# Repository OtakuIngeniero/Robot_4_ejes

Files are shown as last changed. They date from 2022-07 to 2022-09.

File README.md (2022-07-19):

# Robot_4_ejes
proyecto de robot pick n place de cuatro grados de libertad, 250mm de alcance y 400g de carga maxima a maxima extencion

<p align="center">
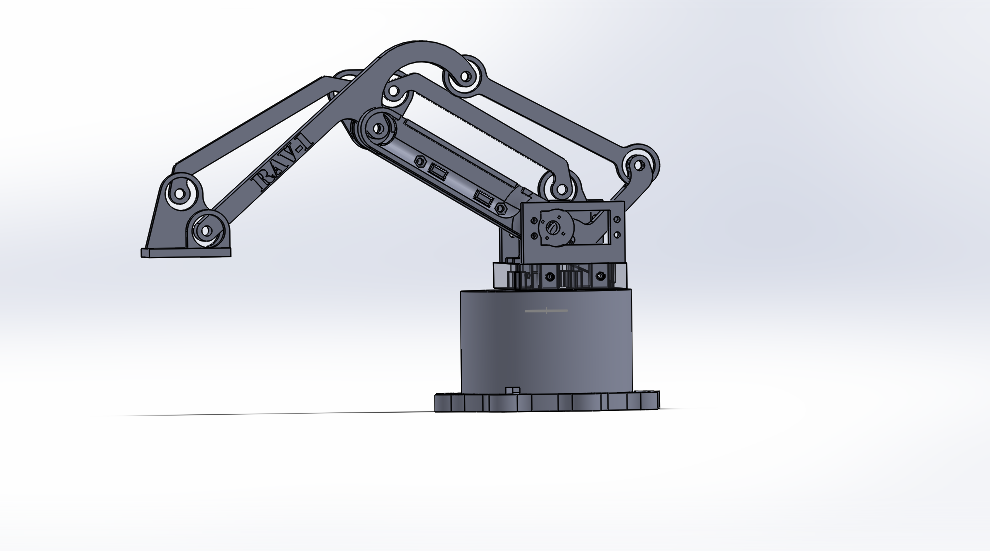
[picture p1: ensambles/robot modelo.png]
hover text
  
</p>

<p align="center">
  
  https://user-images.githubusercontent.com/108755939/179776285-c8175e38-8c07-46ec-a8a5-bc581136b5d1.mp4
  
</p>

- El diseño del robot esta completo y es funcional
- Se midio en un modelo real que cumple las especificaciones planteadas de extencion y carga maxima
- Debido al juego muerto de los motores (1º) el robot tiene en la brida un juego de aproximadamente +-3mm

- Si bien existen muchos controladores para robot mejores y mas completos se me pedia escribir el mio propio para el proyecto, asi que eso hice, el controlador es el modulo "robot", necesita para andar tener instalado sympy

# Lista de compras:

- rodamientos:

15 ----------- Ruleman 6262RS

1 ------------ Ruleman 30202JR /optativo v2 30305

- motores:

3 ------------ Servomotor MG946R

1 ------------ Servomotor SG90

- Controlador:

1 ------------ Arduino nano

- Buloneria:

6 ------------ tornillos de 3/2in con tuercas

18 ----------- tornillos de 1/2in

6 ------------ tornillos de 1in

1 ------------ varilla retificada de 6mm

# TO DO list:
- Darle mas robustez al codigo, principalmente en los puntos no alcanzables
- Hacer un pcb para el arduino porque esta en protoboard
- Comentar y documentar el codigo porque en 1 mes me voy a olvidar de todo

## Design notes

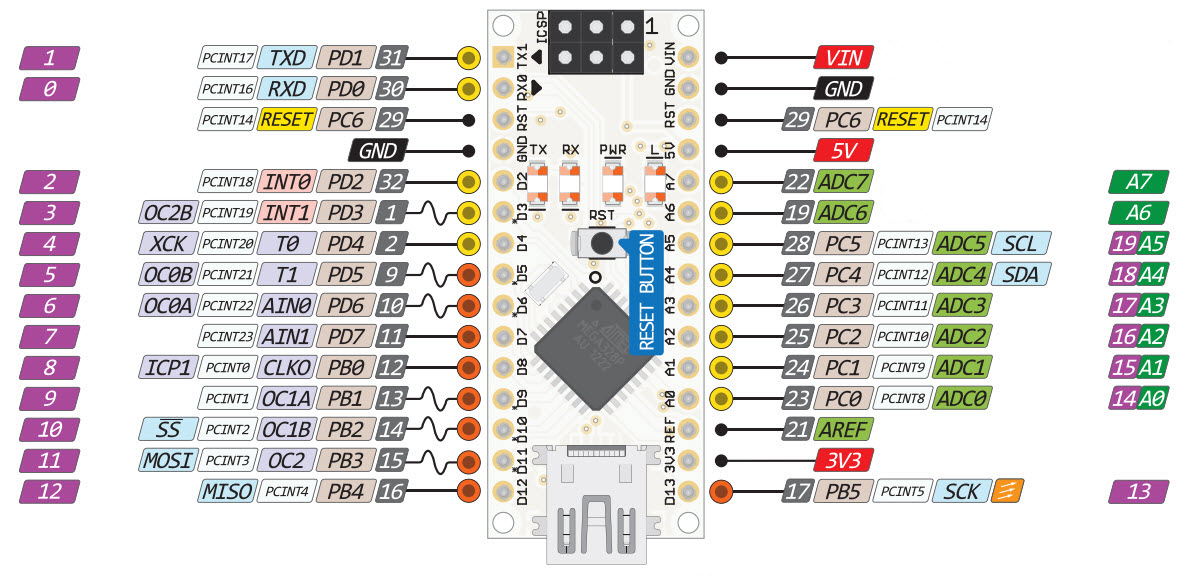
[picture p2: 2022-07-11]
robot irl/arduino nano pinout.jpg

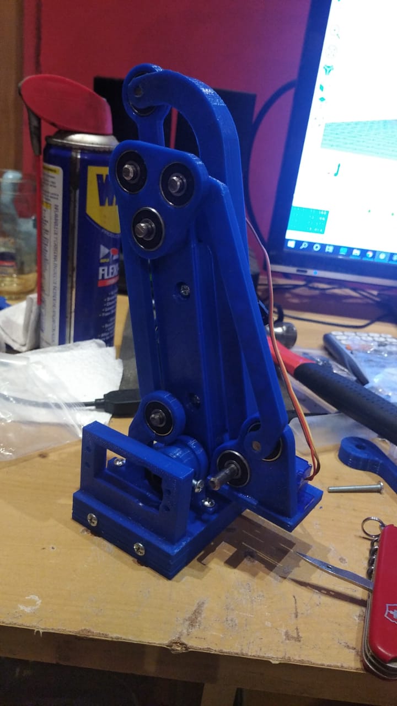
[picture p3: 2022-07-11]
robot irl/img/brazo.jpeg

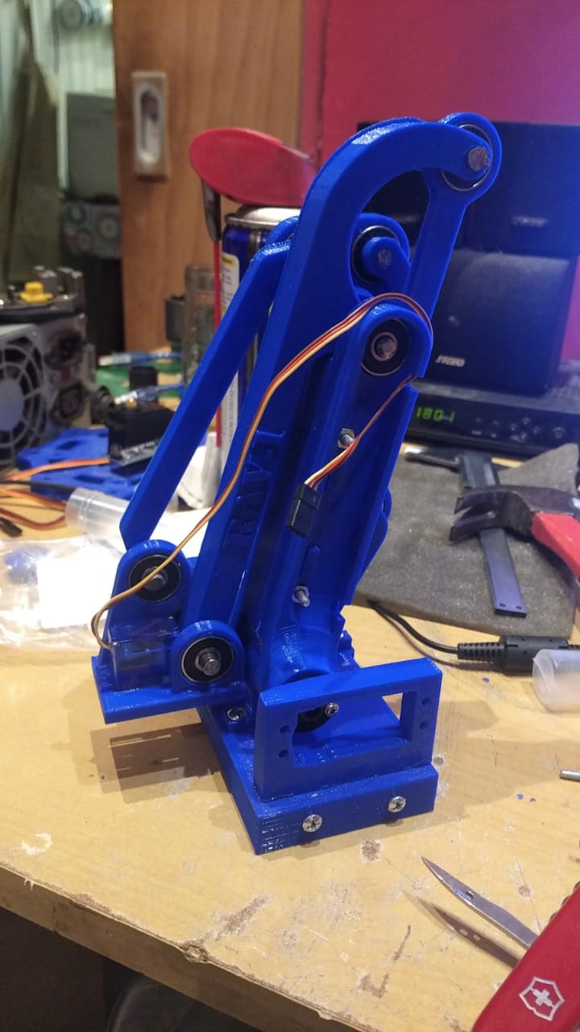
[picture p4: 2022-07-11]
robot irl/img/brazo2.jpeg

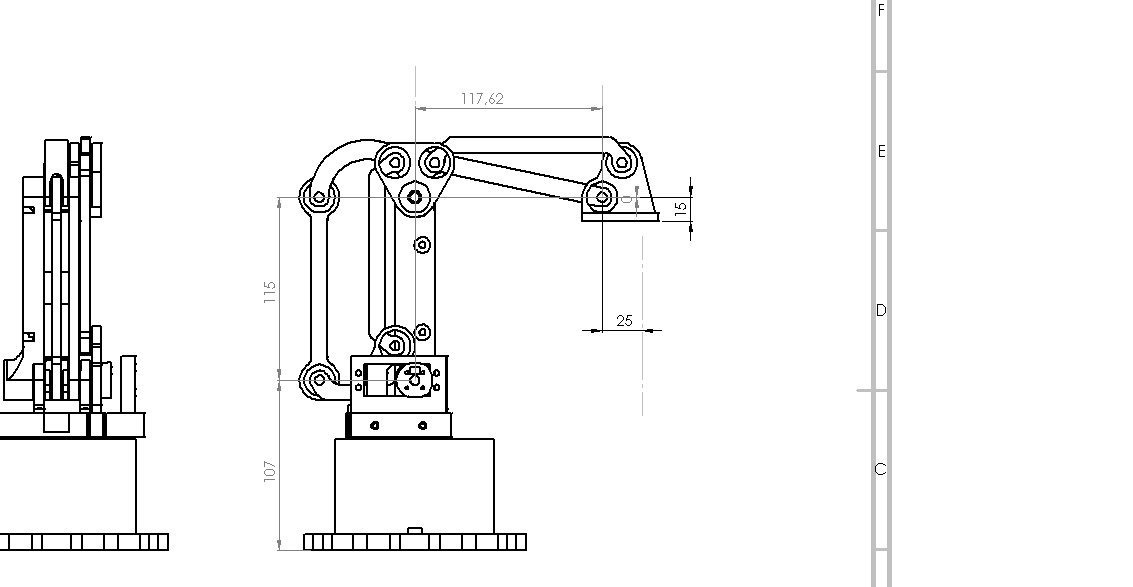
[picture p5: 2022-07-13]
planos/plano_lateral.JPG

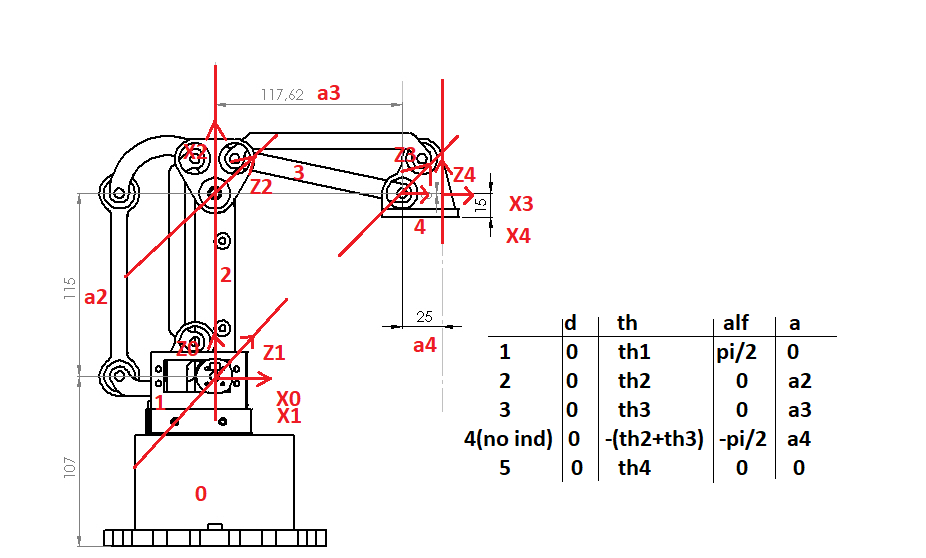
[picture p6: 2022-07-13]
planos/DH_params.png

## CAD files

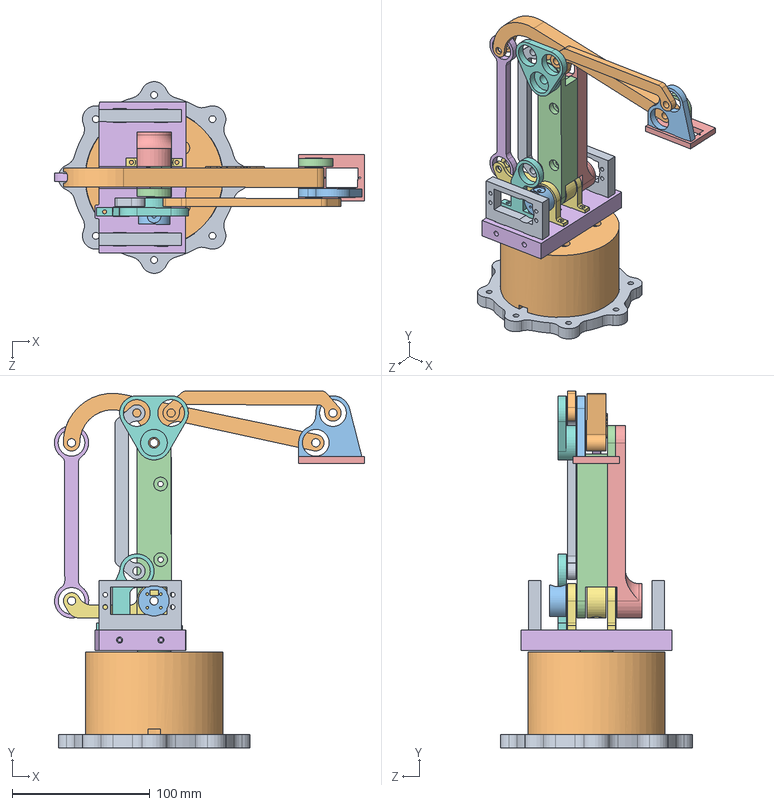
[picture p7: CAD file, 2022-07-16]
ensambles/Ensamble completo.SLDASM
225.7 x 259.7 x 139.3 mm
Base_A
Base_B
Base_C
30202JR
Eje_1_tractor
Eje_1_plataforma
Soporte_eje_2 x 2
Soporte_paralelas
Soporte_motor x 2
Eje_3
Eje_4_A
Eje_4_B
Eje_4_C
Leva_eje_3
Panalca_eje_3
Triangulo
Varilla_115mm
Varilla_117mm
eje_3_tractor
Eje_2_A
Eje_2_B

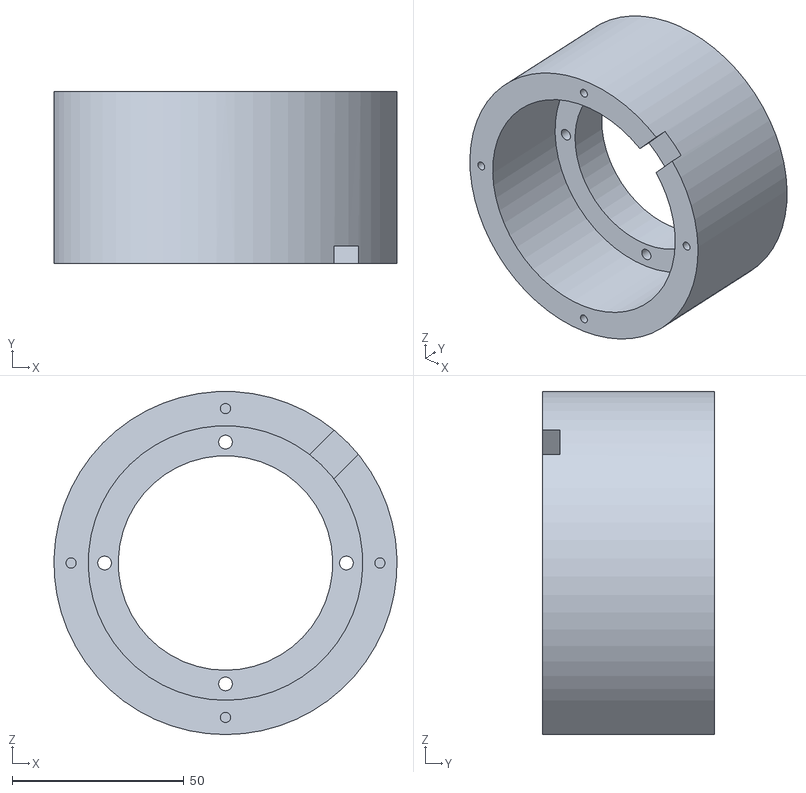
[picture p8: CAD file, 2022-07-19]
imprimibles/base/Base_A_V2.STL
100.0 x 50.0 x 100.0

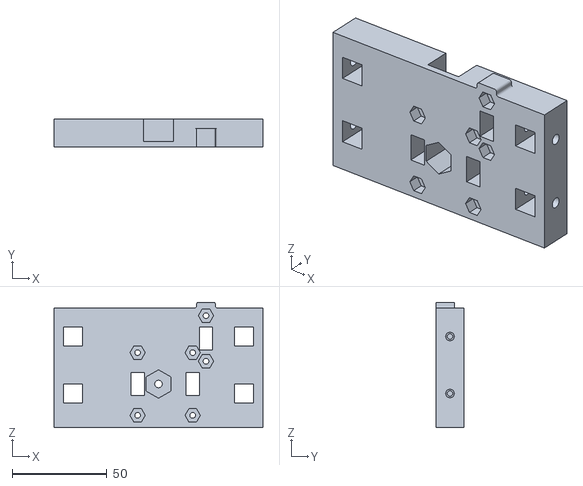
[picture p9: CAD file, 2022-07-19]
imprimibles/eje_1/Eje_1_plataforma_V2.STL
110.0 x 15.0 x 66.0

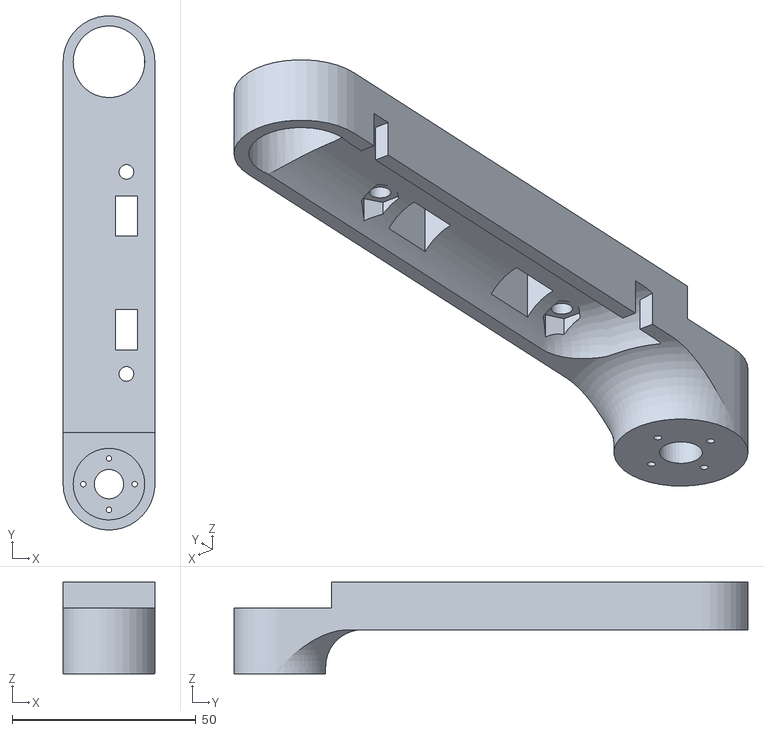
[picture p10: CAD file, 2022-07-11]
imprimibles/eje_2/Eje_2_B_extra_alcance.STL
25.0 x 139.9 x 25.0

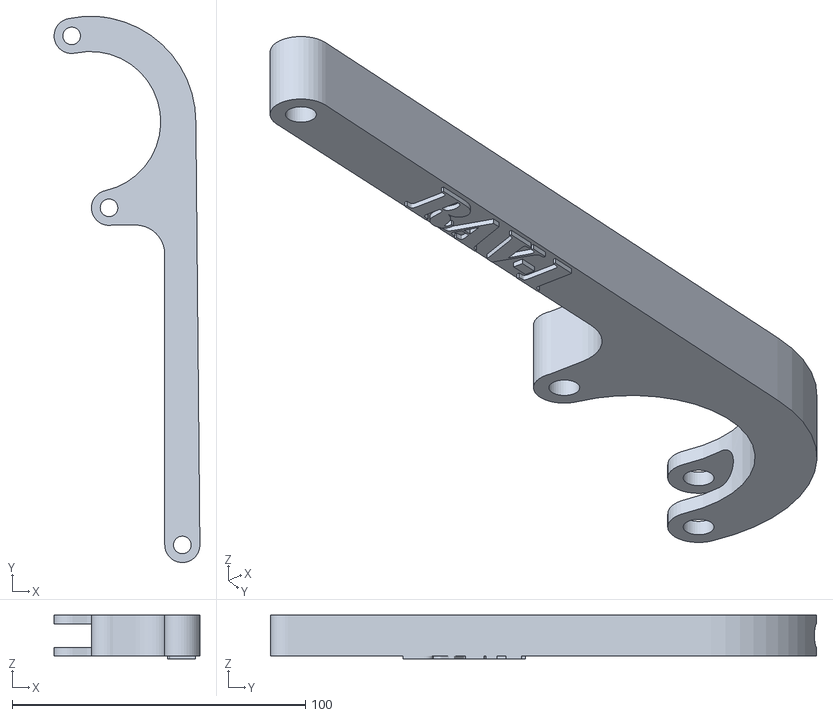
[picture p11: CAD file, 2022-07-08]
imprimibles/eje_3/Eje_3.STL
49.7 x 186.2 x 15.0

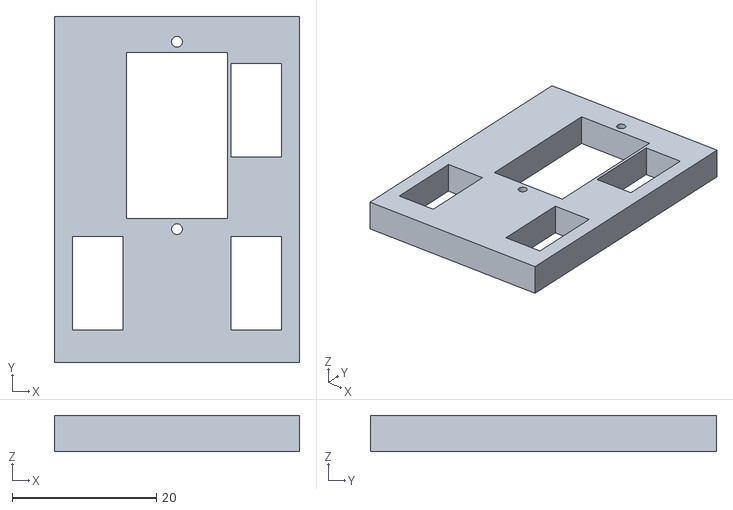
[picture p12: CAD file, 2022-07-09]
imprimibles/eje_4/Eje_4_C.STL
34.0 x 48.0 x 5.00

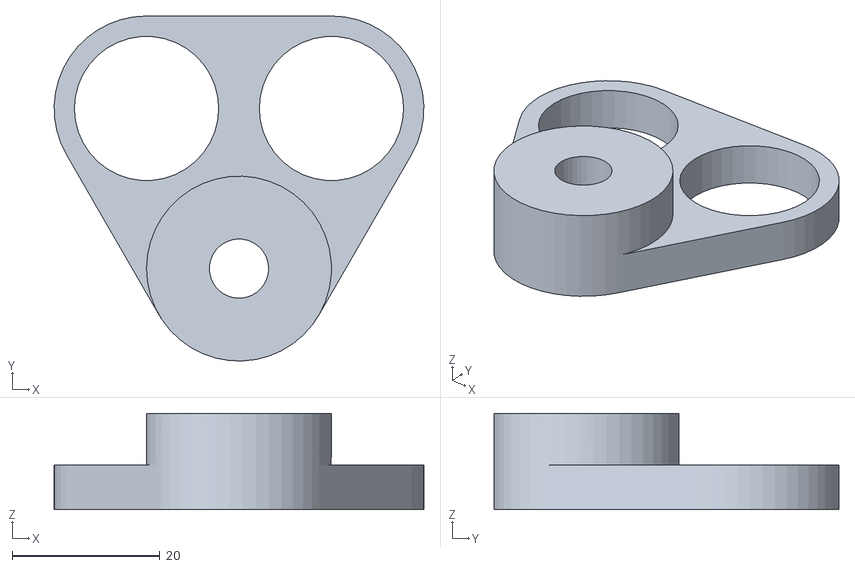
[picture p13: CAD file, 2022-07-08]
imprimibles/paralelas/Triangulo.STL
50.0 x 46.6 x 13.0

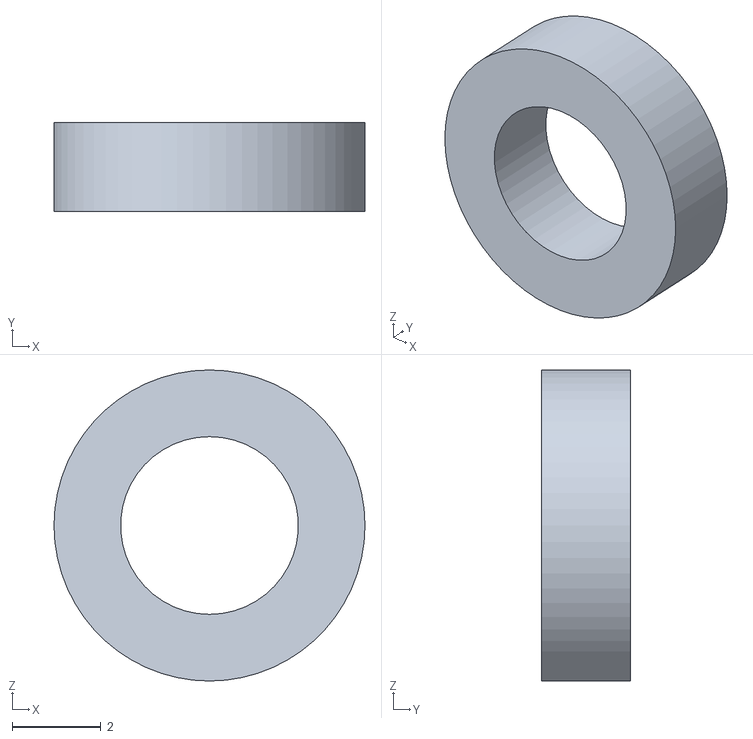
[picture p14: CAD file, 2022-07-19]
imprimibles/separador 2mm.STL
7.00 x 2.00 x 7.00

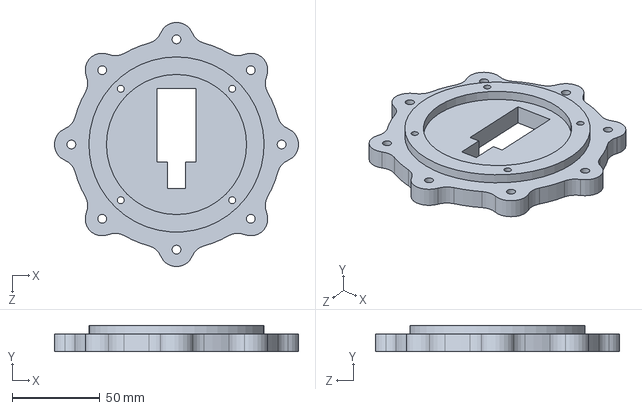
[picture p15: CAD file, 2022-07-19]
piezas/Base_B_V2.SLDPRT
139.3 x 15.0 x 139.3 mm

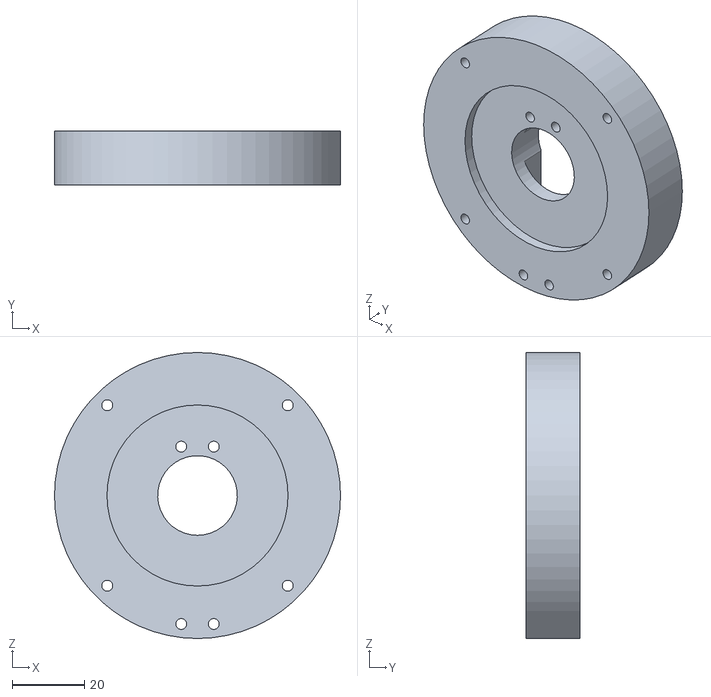
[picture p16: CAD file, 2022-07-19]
imprimibles/base/Base_C_V2.STL
79.0 x 15.0 x 79.0

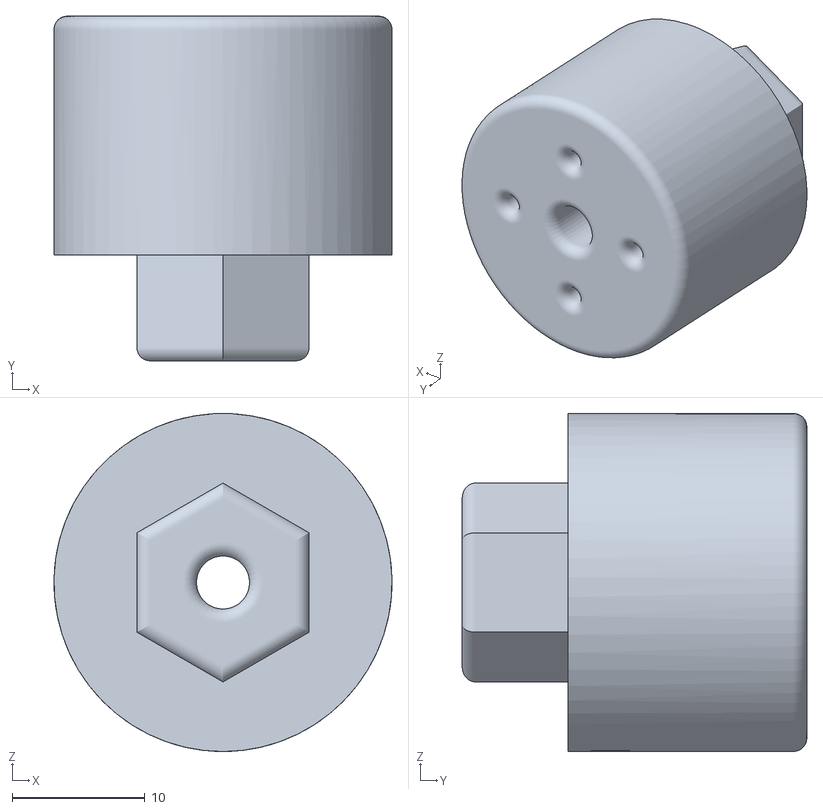
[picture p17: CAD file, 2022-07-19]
imprimibles/eje_1/Eje_1_tractor_V2.STL
25.5 x 26.0 x 25.5

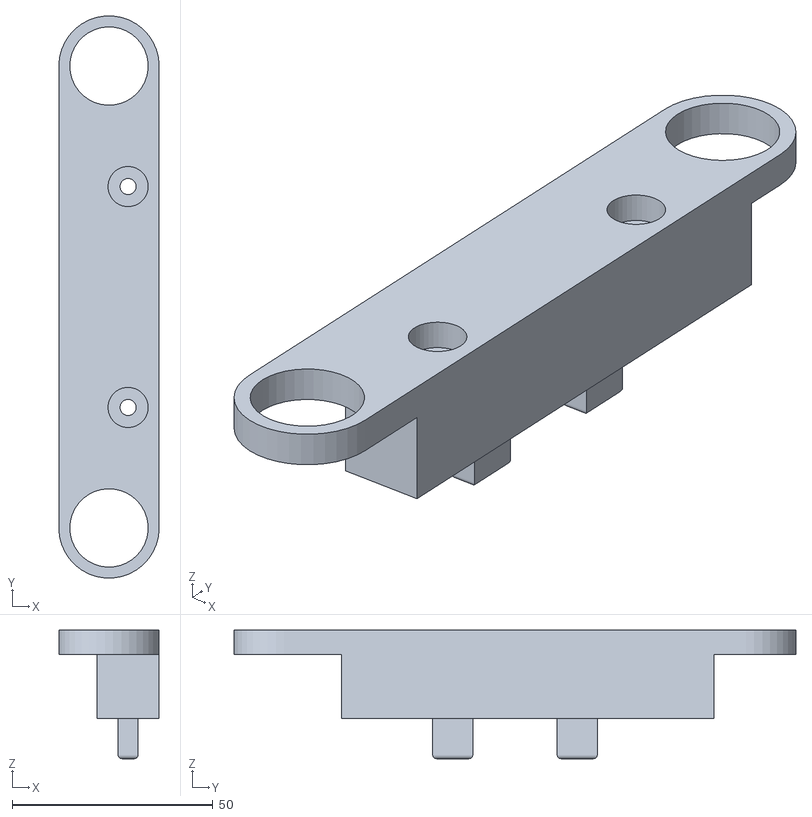
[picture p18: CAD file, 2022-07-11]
imprimibles/eje_2/Eje_2_A_extra_alcance.STL
25.0 x 139.9 x 32.0

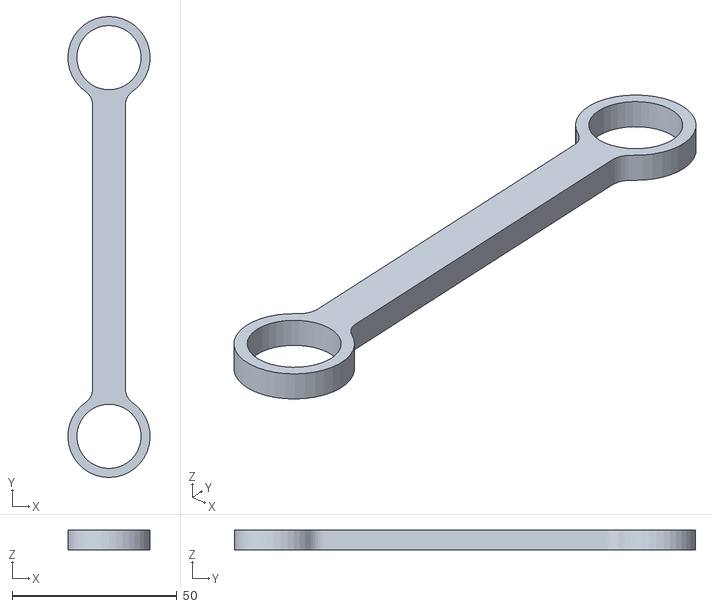
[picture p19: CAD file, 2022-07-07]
imprimibles/eje_3/Leva_eje_3.STL
25.0 x 140.0 x 6.00

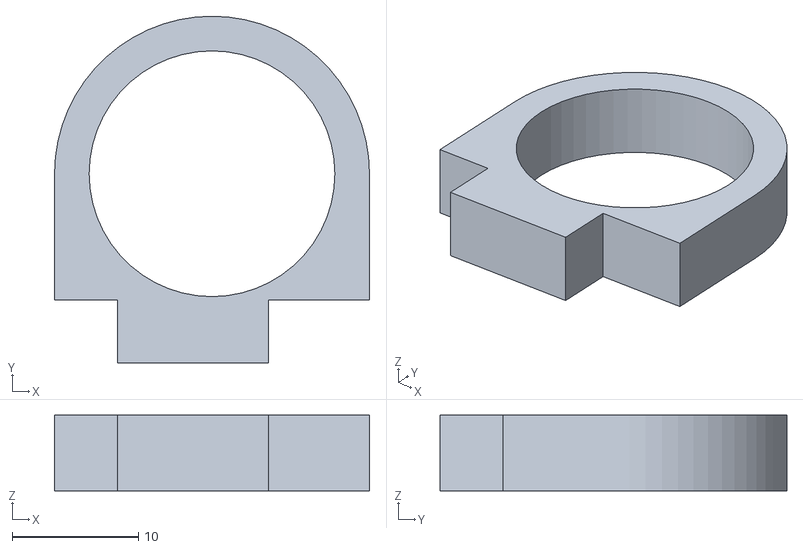
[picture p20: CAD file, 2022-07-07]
imprimibles/eje_4/Eje_4_B.STL
25.0 x 27.5 x 6.00

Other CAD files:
imprimibles/separador 5mm.STL
piezas/Eje_1_tractor.SLDPRT
imprimibles/base/separador_V1-V2.STL
imprimibles/eje_1/Soporte_eje_2.STL
imprimibles/base/Base_B.STL
imprimibles/base/Base_B_V2.STL
imprimibles/base/Base_C.STL
imprimibles/eje_1/Eje_1_plataforma.STL
imprimibles/eje_1/Eje_1_tractor.STL
imprimibles/eje_1/Soporte_motor_d.STL
imprimibles/eje_1/Soporte_motor_i.STL
imprimibles/eje_1/Soporte_paralelas.STL
imprimibles/eje_2/Eje_2.STL
imprimibles/eje_2/Eje_2_A.STL
imprimibles/eje_2/Eje_2_B.STL
imprimibles/eje_4/Eje_4_A.STL
imprimibles/medidor_de_torque.STL
imprimibles/separador_6-10x1 abierta.STL
imprimibles/separador_6-10x1.STL
piezas/Base_A_V2.SLDPRT
piezas/Base_B.SLDPRT
piezas/Base_C.SLDPRT
piezas/Base_C_V2.SLDPRT
piezas/Eje_1_plataforma.SLDPRT
piezas/Eje_1_plataforma_V2.SLDPRT
piezas/Eje_1_tractor_V2.SLDPRT
piezas/Eje_2.SLDPRT
piezas/Eje_2_A.SLDPRT
piezas/Eje_2_A_extra_alcance.SLDPRT
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

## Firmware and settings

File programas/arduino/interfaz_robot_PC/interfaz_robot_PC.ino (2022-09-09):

#include <Servo.h>

Servo eje1;  // crea el objeto servo
Servo eje2;  // crea el objeto servo
Servo eje3;  // crea el objeto servo
Servo eje4;  // crea el objeto servo

int pwm1 = 2;        // uso la pata D2 para enviar el PWM al servo 1
int pwm2 = 3;        // uso la pata D3 para enviar el PWM al servo 2
int pwm3 = 4;        // uso la pata D4 para enviar el PWM al servo 3
int pwm4 = 5;        // uso la pata D5 para enviar el PWM al servo 4
int gripper_out = 6; // uso la pata D6 para el gripper

const int pinLED = 13;
int Q[] = {90,140,40,90};
int gripper = 0;
int motors = 0;
// home <90:140:40:0>
int QlimPos[] = {180,152,40,180,0};//Q3 tambien tiene de limite Q2-algo porque como estan invertidos es complicado sacar la relacion Q2=70->Q3=45
int QlimNeg[] = {0,54,150,0,0};

const byte buffSize = 40;
char inputBuffer[buffSize];
const char startMarker = '<';
const char endMarker = '>';
byte bytesRecvd = 0;
boolean readInProgress = false;
boolean newDataFromPC = false;

float inicio =0;
float fin = 0;

void setup(){
  eje1.attach(pwm1);  // vinculo los servos
  eje2.attach(pwm2);
  eje3.attach(pwm3);
  eje4.attach(pwm4);

   
  Serial.begin(115200);
  Serial.write(".");
  pinMode(pinLED, OUTPUT);
  pinMode(gripper_out, OUTPUT);
  }


void loop(){
  inicio=millis();                              // establesco un Ts de 20ms
  fin= inicio+20;

  
  
  if (Serial.available()>0) 
  {
    digitalWrite(pinLED, HIGH);
    SerialEvent();
    digitalWrite(pinLED, LOW);
    Serial.write(".");
    // actualizo los servos 
    if (motors == 1)
    {
      eje1.write(Q[1]); 
      eje2.write(Q[2]); 
      eje3.write(Q[3]); 
      eje4.write(Q[4]);
    }
  }


  digitalWrite(gripper_out, gripper);
  while (fin > millis())  {}
}

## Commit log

2022-07-05 -V0.0.1
    -backup de la version 0.0.1 del robot aun sin terminar el modelo
    [Base_B_v0_0_1.SLDPRT, Base_B_v0_0_2.SLDPRT, Eje_2_V0_0_1.SLDPRT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]
2022-07-05 - add
    - se agregaron piezas de la base
    [Base_B_v0_0_2.SLDPRT, Base_C_v0_0_2.SLDPRT]
2022-07-05 - add
    - Agregado de la parte inferior de la base
    [Base_A_v0_0_1.SLDPRT, Base_C_v0_0_2.SLDPRT]
2022-07-06 -add
    -se agrego la plataforma
    [Eje_1_plataforma_V0_0_1.SLDPRT]
2022-07-06 -add
    -se agrego un ensamblaje con el brazo completo
    [Ensamble completo.SLDASM]
2022-07-06 -update v1.0.0
    - version 1.0.0 del robot simulada (mecanica)
    -hay que corregir el anclaje del paralelismo
    -hay que empolinar los nombres de las piezas
    -hay que mejorar el encastre de las partes del eje 4
    [30202JR.SLDPRT, Base_C_v0_0_2.SLDPRT, Eje_1_plataforma_V0_0_1.SLDPRT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]
2022-07-07 -update
    - se comenzaron a hacer los std para imprimir
    - tambien se reparo la parte del soporte de las paralelas
    [Base_A.STL, Base_A_v0_0_1.SLDPRT, Base_B.STL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]
2022-07-07 -renombrado de piezas -v1.0.0
    -se cambio el nombre de las piezas por prolijidad
    [30202JR.SLDPRT, Base_A.SLDPRT, Base_B.SLDPRT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]
2022-07-07 -update v1.0.2
    -se agregaron todas las piezas para imprimir
    -se arreglo la distancia entre el eje 4 y los soportes del eje 2 cuando el brazo esta plegado
    [Eje_1_plataforma.STL, Eje_2.STL, Eje_3.STL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]
2022-07-07 -v1.0.3 -facilitar impresion
    se cambiaron los encastres de los soportes para que sea mas facil de imprimir
    [Eje_1_plataforma.SLDPRT, Eje_1_plataforma.STL, Ensamble completo.SLDASM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]
2022-07-07 -v1.0.4 ajuste de alojamientos
    -se ajustaron los alojamientos de los rodamientos
    [30202JR.SLDPRT, Base_A.SLDPRT, Base_A.STL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]
2022-07-08 -V1.1.0 cambio del eje 2
    -se modifico el eje 2 para imprimirlo en 2 partes
    [Base_B.SLDPRT, Base_B.STL, Eje_1_tractor.SLDPRT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]
2022-07-09 -V1.1.1 -encastres y mediciones
    -se mejoraron aun mas algunos encastres de piezas
    -se agregaron una palanca de 10cm y un codigo en arduino para medir el torque de los motores
    [Eje_1_plataforma.SLDPRT, Eje_1_plataforma.STL, Eje_4_C.SLDPRT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]
2022-07-11 -v1.1.2 se agregaron piezas opcionales y codigo
    -se agregaron piezas opcionales al eje 2 para incrementar la extencion
    -se agrego codigo para controlar el robot en modo joggin manual usando potenciometros
    [Eje_2_A.SLDPRT, Eje_2_A_extra_alcance.SLDPRT, Eje_2_A_extra_alcance.STL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]
2022-07-11 -v1.1.2 -agregado de imagenes chetas del robot irl
2022-07-13 -vh1.1.2 -vs0.0.1
    -se hizo una interfaz con arduino
    -se comenzo con el controlador en python
    -se hizo un modelo cinematico del robot
    [plano_lateral.SLDDRW]
2022-07-16 -vh1.2.0 -vs0.0.2
    -modifique algunas piezas para poder usar tornillos mas cortos
    -se agregaron espaciadores que se pueden poner luego de armado el robot
    -ya anda con una version fea de movimientos joint
    -el stream de datos ahora permite control de velocidad desde la pc
    [Base_B.SLDPRT, Base_B.STL, Base_C.SLDPRT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]
2022-07-19 -vh1.3.0 -vs0.1.0
    -muchos fixes en el hard, se hizo tambien una version optativa con el rodamiento 30305
    -el soft se corrigieron los saltos y ya anda con movimientos joint y lineales, ya se envian ordenes de encendido y apagado de los motores y el gripper
    - importando el modulo "robot" se puede hacer un programa para el robot usandolo de la misma manera que cualquier robot comercial (masomenos)
    [Base_A_V2.SLDPRT, Base_A_V2.STL, Base_B_V2.SLDPRT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]
2022-07-19 ya anda el robot wiii
2022-07-19 -vh1.2.0 -vs0.0.2 -se agrego el script de revolver
2022-09-09 agregado de demos
    se agregaron scripts de demos del uso del robot
